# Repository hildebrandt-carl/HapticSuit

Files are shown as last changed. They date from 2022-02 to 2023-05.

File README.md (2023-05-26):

# Mimicking Real Forces on a Drone Through a Haptic Suit to Enable Cost-Effective Validation

Robots operate under certain forces that affect their behavior. For example, a drone meant to deliver packages must hold its pose as long as it operates under its weight and wind limits. Validating that such a drone handles external forces correctly is key to ensuring its safety. Nevertheless, validating the system's behavior under the effect of such forces can be difficult and costly. For example, checking the effects of different wind magnitudes may require waiting for the matching outdoor conditions or building specialized devices like wind tunnels. Checking the effects of different package sizes and shapes may require many slow and laborious iterations, and validating the combinations of wind gusts and package configurations is often hard to replicate. This work introduces a framework to overcome such challenges by mimicking external forces exercised on a drone with limited cost, setup, and space. The framework consists of a haptic suit device consisting of directional propellers that can be mounted onto a drone, a component to transform intended forces into setpoints for the suit's directional propellers, and a controller for the suit to meet those setpoints. We conduct a study to assess the framework's capabilities under multiple scenarios involving various forces. Our findings show that the haptic suit framework can recreate real-world forces on the drone with acceptable precision.

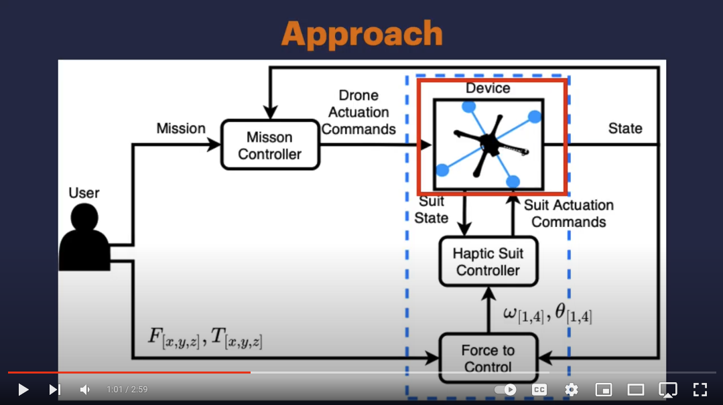
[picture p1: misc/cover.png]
Video (https://youtu.be/5_QmRLWMhes)


## Prerequisites

### Hardware

This software was developed, run and test on the following machines. 

| Computer | CPU | CPU Cores | RAM | Operating System  |
|---|---	|---	|---	|--- |
| Computer 1 | AMD Ryzen Threadripper 3990X | 128 | 128 GB | Ubuntu 20.04 |
| Computer 2 | Intel Core i7-10750H | 12 | 16 GB | Ubuntu 20.04 |

### Software

We require that you have [ROS Noetic](http://wiki.ros.org/noetic/Installation) to operate the drone. We require that you use the [Arduino IDE](https://www.arduino.cc/en/software) for flashing the haptic suit controllers. Finally we require that you have [SOLIDWORKS](https://www.solidworks.com) and a 3D printer for printing the arms of the haptic suit. Finally we require that you have [Matlab](https://www.mathworks.com/products/matlab.html) for computing the inverse kinematics.

## Getting Started

| Component 	| Description 	| Link 	 |
|---	|---	|--- |
| Kinematics 	 | This will describe how we implemented the kinematics and includes Matlab code used to solve the inverse. 	| [README.MD](./kinematics/README.md) 	|
| Physical Design | This includes the designs for the physical arms, battery holders, and pendulum used in our study. 	| [README.MD](./physical_design/README.md)  |
| Drone Workspace 	| This has the software used to fly the drone in each of the scenarios listed in the paper. 	| [README.MD](./drone_ws/README.md) |
| Firmware 	| This describes how to flash the firmware used by the haptic suit | [README.MD](./firmware/README.md) 	 |
| Paper 	 | Includes the paper published at [ICRA 2023](https://www.icra2023.org) | [Paper.pdf](./paper/HapticSuit.pdf) 	|

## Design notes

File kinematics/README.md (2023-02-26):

# Kinematics

This contains the kinematics used convert a force into 4 motor speeds and directions. 

## Derivation

This contains the workings out for how the equations were derived. We started first using a single motor, then computing how it would change if it were allowed to rotate. Next we looked at how 2 motors would behave, and then finally 4 motors. The final equations are shown below:

4 Motors

## Matlab

Next we include the code used to compute the inverse kinematics. To run this open it in matlab and click the green arrow.

### Plotter

Finally we include the code used to plot the force and motor combinations. To run this use the following:

```bash
python animtated_plot.py
```

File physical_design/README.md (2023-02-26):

# Physical Design

This provides both the SOLIDWORKS and SDL files used to 3D print our haptic suit. Each of these were developed to connect DJI Flame Wheel F450. We provide the following:
* Haptic suit arm
* Battery holder
* Pendulum

## Haptic Suit Arm

The blue dashed lines show two arms. To print each arm you can use the following components:

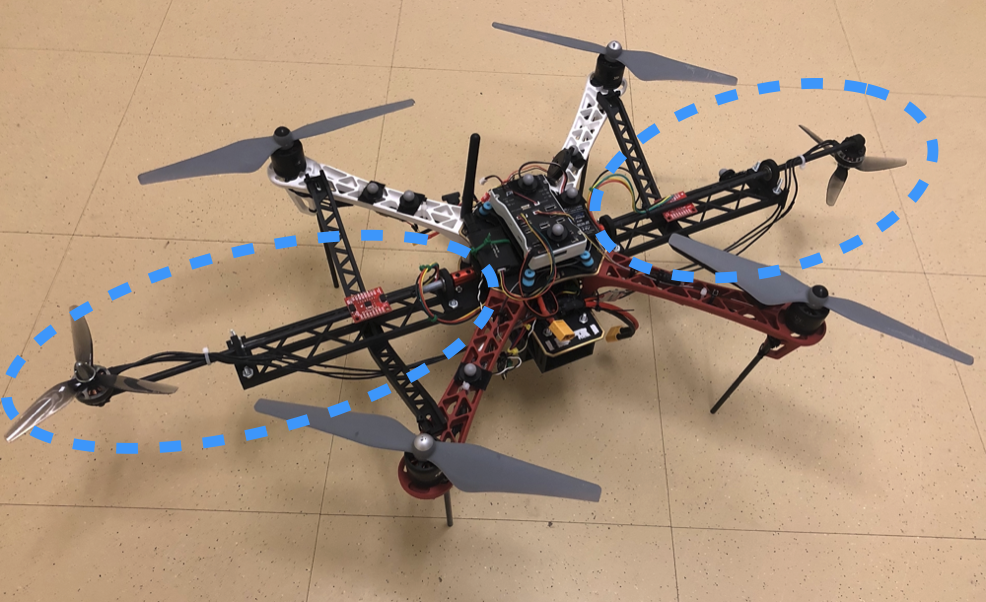
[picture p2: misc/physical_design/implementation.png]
Arms


### Arm

This is the main structure that extends outwards from the body of the drone.

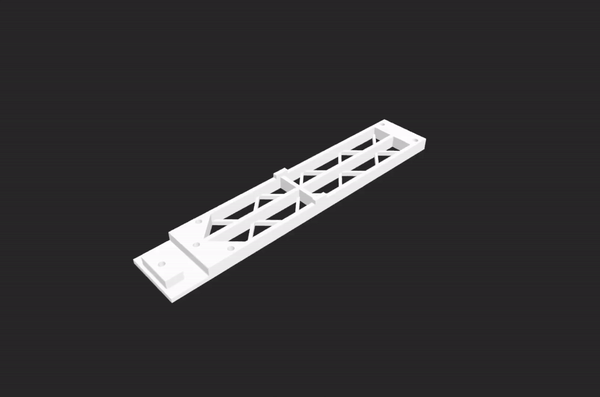
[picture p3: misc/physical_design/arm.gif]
Arm


### Arm Clip

This clips between the arm and the frame, to lock the arm to the frame of the quadrotor.

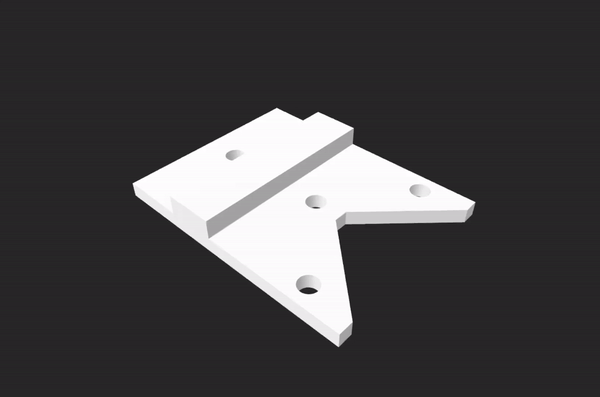
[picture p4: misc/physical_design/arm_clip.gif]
Arm Clip


### Arm Support

This connects to each of the quadrotor arms to add additional support

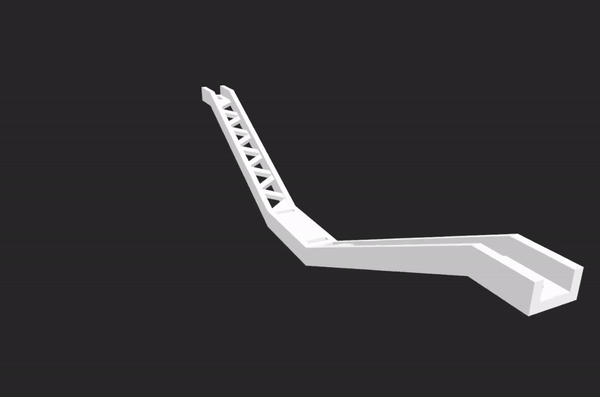
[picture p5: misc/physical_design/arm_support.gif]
Arm Support


### Arm Motor Holder

This sits at the beginning of the arm, and holds the motor used to rotate the direction of the force generated.

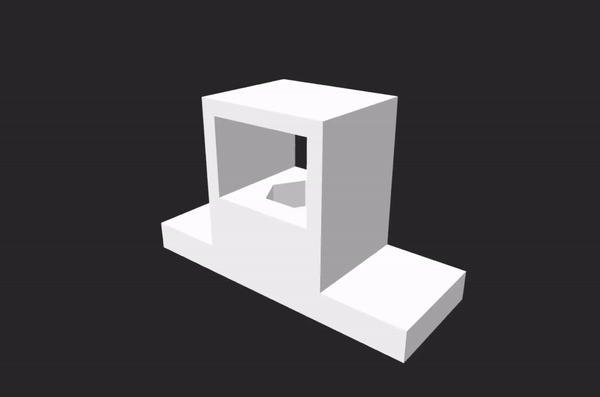
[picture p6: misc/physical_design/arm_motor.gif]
Arm Motor Holder


## Battery Holder

The battery holder sits underneath the drone and holds the battery for both the haptic suit and the quadrotor.

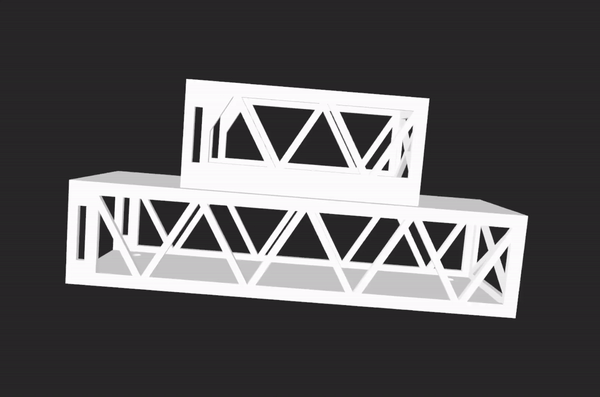
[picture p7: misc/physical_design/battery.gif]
Battery Holder


## Pendulum

The pendulum used in the study was also 3D printed. It consists of two parts. 

### Hinge

First the hinge which is that attached to the drone.

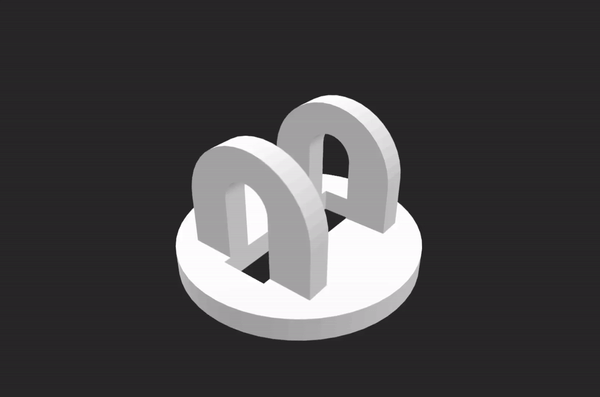
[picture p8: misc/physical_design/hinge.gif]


### Connector

Second the connector which sits inside the hinge.

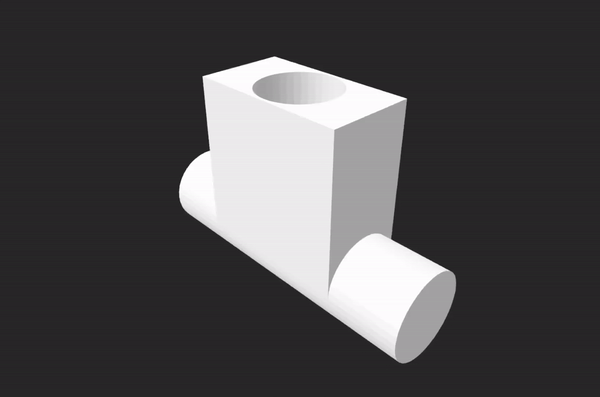
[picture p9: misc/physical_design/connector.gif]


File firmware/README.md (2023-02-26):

# Firmware

To flash the firmware you need to use the [Arduino IDE](https://www.arduino.cc/en/software). This also includes our PID class shown below:

```c
#include <math.h>
#include <Arduino.h>

// A class to compute the control signal
class PID{
  private:
    float Kp ;
    float Ki ;
    float Kd ;
    float dt ;
    float integral;
    float previous_error;

  public:

  // Constructor
  PID()
  {
    Kp = 0;
    Ki = 0;
    Kd = 0;
    dt = 0;

    // Variables used by the controller
    integral = 0;
    previous_error = 0;
  };

  // Constructor
  PID(float Kp_in, float Ki_in, float Kd_in, float rate_in)
  {
    Kp = Kp_in;
    Ki = Ki_in;
    Kd = Kd_in;
    dt = 1.0  / rate_in;

    // Variables used by the controller
    integral = 0;
    previous_error = 0;
  }

  // A function to set the parameters
  void set_parameters(float Kp_in, float Ki_in, float Kd_in, float rate_in)
  {
    Kp = Kp_in;
    Ki = Ki_in;
    Kd = Kd_in;
    dt = 1.0  / rate_in;
  }

  // A function to compute the control signal
  float get_output(float setpoint, float current_output)
  {

    // Create the output
    float output;

    // Run the controller
    float error = setpoint - current_output;
    integral = integral + error * dt;
    float derivative = (error - previous_error)/dt;
    output = Kp*error + Ki*integral + Kd*derivative;
    previous_error = error;

    // Return the output
    return output;
  }
  
};
```

This was used to control both the angle of each of the arms. Please refer to the Arduino documentation for further information on how to flash each of the different boards.

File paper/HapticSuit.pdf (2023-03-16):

## Mimicking Real Forces on a Drone Through a Haptic Suit to Enable Cost-Effective Validation

Carl Hildebrandt¹

, Wen Ying¹

, Seongkook Heo¹

, and Sebastian Elbaum¹

Abstract— Robots operate under certain forces that affect their behavior. Consider, a drone meant to deliver packages must hold its pose as long as it operates under its weight and wind limits. Validating that such a drone handles external forces correctly is key to ensuring its safety. Nevertheless, validating the system’s behavior under the effect of such forces can be difficult and costly. For example, checking the effects of different wind magnitudes may require waiting for the matching outdoor conditions or requiring wind tunnels. Checking the effects of different package sizes and shapes may require many slow and laborious iterations, and validating the combinations of wind gusts and package configurations is often hard to replicate. This work introduces a framework to overcome such challenges by mimicking external forces exercised on a drone with limited cost, setup, and space. The framework consists of a haptic suit device with directional propellers that can be mounted onto a drone, a synthesizer to transform intended forces into setpoints for the suit’s directional propellers, and a controller for the suit to meet those setpoints. We conduct a study to assess the framework’s capabilities under multiple scenarios involving various forces. Our findings show that the haptic suit framework can recreate real-world forces on the drone with acceptable precision.

I. INTRODUCTION
Drones are incredibly versatile, allowing them to complete a multitude of missions in a variety of environments. They can carry sensors and objects [1], [2], balance inverted pendulums [3], [4], juggle balls [5], [6], grasp or push objects [7], [8], or take off from underwater [9]. Throughout all these missions, external forces are exerted on the drone. Carrying weights adds a downwards force, hanging pendulums introduce a swinging force, juggling balls create an intermittent impact force, grasping objects adds a downwards and rotational force, and taking off from underwater adds a resistive force that is removed once in the air.
Validating that drones can adequately behave under those external forces is critical to ensure their correct and safe operation. Such validation takes multiple forms, from model simulation, which offers the opportunity to quickly test many variants of the system and approximations of the forces in the environment, to field tests that exercise the entire system in a limited number of real environments with real physical forces. In this work, we focus on the challenge of conducting full system tests carried out in both a lab and in the field. Validating the effect of external forces on drones brings significant challenges. Consider a drone that must hold its pose while delivering cargo. First, precisely validating the

1University of Virginia, USA {hildebrandt.carl, wy7yv, seongkook, selbaum}@virginia.edu
This work was funded in part through NSF grants #1924777 and AFOSR grant #FA9550-21-1-0164.

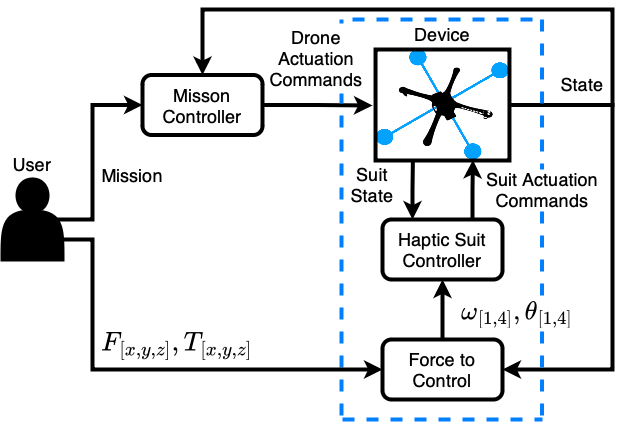
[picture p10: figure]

Fig. 1: Overview of the Haptic Suit Framework

effects of wind would require specialized mechanisms like wind tunnels. Second, validating the space of behaviors would require validating various cargo configurations (e.g., weight, shape). This can be laborious as testers must often set each scenario manually. Third, some forces are extremely difficult to replicate, such as those caused by the subtle combination of gusts of wind and cargo configuration. These challenges make drone behavior validation under external forces costly, difficult, and often infeasible.
In this work, we introduce a framework to address these challenges. Inspired by haptic feedback in interactive systems that simulate forces to provide immersive experiences to users [10], [11], this framework recreates forces on the drone to replicate real-world scenarios. Figure 1 provides an overview of the framework and its three key components:
1) an electro-mechanical device that attaches to the drone under test to provide directional propellers that can generate a rich space of forces and torques; 2) a synthesizer that transforms user-specified force F[x,y,z] and torque T[x,y,z]

functions
into a set of target motor speeds ωi and angles θi for each motor i, using the inverse kinematic equations of the suit; and
3) controllers that read the state of the suit and the drone and use the ωi and θi as setpoints to actuate the suit propellers to match those targets.
The contributions of this work are:
- An innovative concept connecting drone validation and haptic feedback to induce external controlled forces.
- A framework that enables the exertion of a rich set of programmable forces for the validation of drones.
- A study showing that the haptic suit framework can successfully replicate forces from 5 distinct real scenarios.

II. RELATED WORK
Several approaches exist to exercise and manipulate specific external forces on drones. For example, to mimic wind forces, various forms of fans [12], and wind tunnels [13], [14], [15] have been proposed, offering trade-offs between cost, flexibility, and accuracy in the forces being exercised. Similarly, to mimic payloads, it is relatively common to build devices that enable the attachment of different masses with varying volumes [16], [17]. In this case, the level of control can be accurate but often requires a manual setup [18]. Beyond simple forces, we find that general mechanisms for applying forces to a drone are lacking.
In this paper, we aim to accurately mimic more complex external forces without needing expensive setups and laborious procedures. Although not pursuing the same goals, the closest line of work comes from the variety of testbeds meant to support drone development [19], [20], [21], [22], [23]. This work aims to secure the drone such that it can not crash while allowing for some form of movement. For example, Ding et al. proposed using a humanoid arm to hold a drone while it is flying. The goal was to secure the drone while minimizing the effect of this connection [23]. While the purpose of this work was not to exert forces on the drone, one could imagine that with adjustments to the controller function, as well as the development of a new set of kinematics, one could recreate larger forces with precision. Still, these devices are complex and expensive, and for most of the forces we intend to mimic, it would be bounded by the arm’s reach, degrees of freedom, and velocities, while our haptic suit does not have those limitations.
Another related line of work that in part inspired this work is in the area of haptics. Researchers have shown that propeller-based propulsion can be used to produce highfidelity directional force feedback and provide realistic force feedback to its users [10], [11]. However, these methods are designed for handheld use, and their use for robot testing has not been investigated. The closest line of work mimics real sensor values on drones to provide a mix of real world and simulated sensor data [24], [25], [26]. However, this work lacks the ability to exert actual forces onto the drone.

III. FRAMEWORK
The framework aims to mimic the forces a drone may experience during flight, enabling engineers to validate their drones under various scenarios more efficiently, quickly, and easily. We now describe its key components in more detail.
A. Haptic Suit Device
The following requirements guided the haptic suit design. First, the device needed to generate forces with a wide range of magnitudes and directions to support many scenarios (including the ones we later studied). Second, the device needed to mount on the host drone without any point of contact with other external entities in order to reduce flying constraints or interference. Third, the device needed to minimize the disturbance to the drone’s normal behavior to avoid failures that the introduction of the suit may cause.

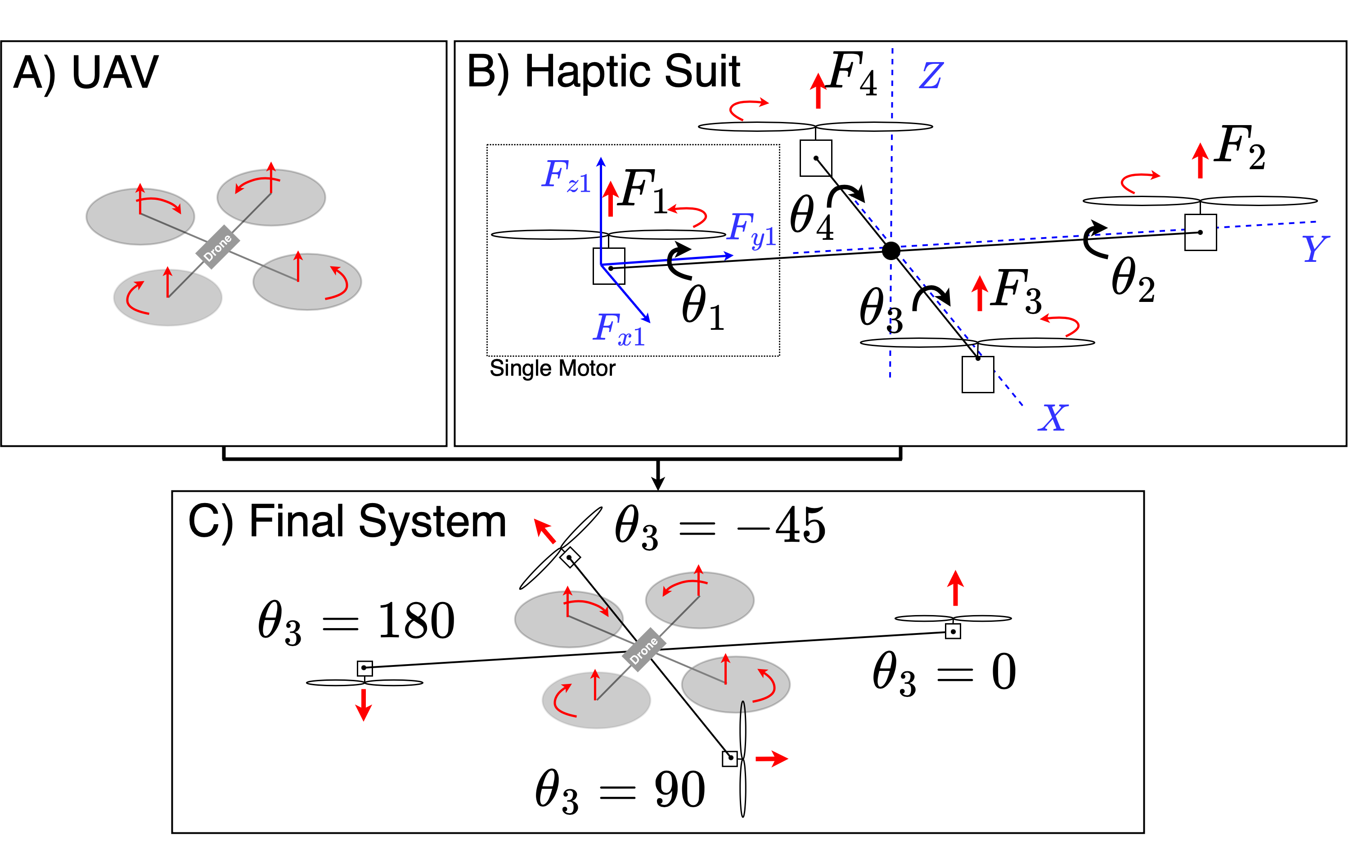
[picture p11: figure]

Fig. 2: Quadrotor, Haptic-Suit, and Haptic-Suit integrated with Quadrotor (grey circles represent quadrotor propellers).

The suit design follows from those requirements. Conceptually, the suit is elegant in its simplicity in that it adopts the host-drone structural design. Without loss of generality and to facilitate the explanation, we exemplify the integration of the haptic suit to a quadrotor as shown in Figure 2. For a quadrotor, shown in Figure 2-A, the suit device consists of four arms, each one with a rotor at its end, as shown in Figure 2-B, reflecting the design of the drone. In the suit, each of the i (i = 4 for quadrotor) rotor’s thrust Fi and torque values Ti can be independently controlled by varying the motor speed ωi

. However, unlike a typical drone where Fi

is
always perpendicular to the drone, the suit can independently rotate each arm by θi
through additional motors at the base of each arm. To allow for precise control, each arm is fitted with an IMU reporting its attitude. This allows us to vary the magnitude of Fi and Ti by varying ωi

, as well as vary
the direction by varying θi
, to create a wide range of forces on the drone regardless of the drone’s current pose.
The integration of the haptic suit and drone is shown in Figure 2-C. The haptic suit is mounted onto the drone with a shift of 45 degrees. This integration meets our requirements in the following ways. First, as each arm has a motor that can independently rotate, it can generate a wide range of forces, allowing for the simulation of a wide range of scenarios. Second, the suit is not attached to anything but the drone, thus not limiting the drone to any specific environment. Third, the suit is symmetrical, lightweight, and has arms that protrude out further than the drone’s arms. This minimizes the changes in both the total and center of mass of the drone while also minimizing interference among airflow through propellers. These design choices reduce the chance that the suit will affect the normal behavior of the drone.
The conceptual design simplicity offers a rich space of trade-offs that will determine the magnitude of the forces that the suit can generate. For example, more powerful motors can generate greater forces. However, their weight, the weight of the arms required to support them, and the battery requirements may undermine some of the forces they can generate and the preciseness of the overall force manipulation. The arms’ length and rotational speed can also affect the type and magnitude of forces that can be applied. This also indirectly affects the airflow of the other drone’s rotors. The profile of all these elements can affect the dynamics of the drone, from adding weight to changing the drag coefficients. We will discuss the particular choices we made for one instantiation of the framework under Section III-F.
B. Force to Control Set Points

Given a haptic suit device, the framework must convert a set of user-defined forces F[x,y,z] and torques T[x,y,z]

into a
set of motor speeds ω[1,4] and rotations θ[1,4]
. For example,
if a user wants to simulate carrying a package, which is equivalent to applying negative force in the Z direction (−Fz), we would need all motors to spin at equal speeds (ω1 = ω2 = ...) such that they generate a force of the correct magnitude (Fz). Furthermore, each of the motors would also need to be pointing directly downwards (θ[1,4] = 180), so that the direction of the force is in the same direction as gravity (−Fz) to exert the same force as a package. Similarly, if a user wants to mimic a horizontal wind with a force Fy, whose magnitude is the same as that of the first example, then motors 2 and 3 would need to create forces in the Fy plane by rotating (θ[3,4] = 90), and each would need to operate at double the speed of the first example to compensate for the lack of motors 1 and 2.
To perform such conversion computations, we define a set of kinematic equations for the haptic suit. Consider motor1 in Figure 2-B, with target speed ω1 and rotation θ1. The force F1 and torque T1 generated by that motor are F1 = kf × ω1 and T1 = km×ω1 where kf and km are the proportionality constants for thrust and moments respectively [27]. Since the capability to rotate the motor affects the forces and torques direction, we must decompose F1 and T1 into (Fx1,Fy1,Fz1) and (Tx1,Ty1,Tz1). Equations 1 showcase the decomposition of F, with similar equations holding for T.

Fx1 = −F1 ×sin(θ1); Fy1 = 0; Fz1 = F1 ×cos(θ1) (1)

We can now generalize these equations to a full suit as per Equations 2.

Fxi = −Fi ×sin(θi);Fyi = 0;Fzi = Fi ×cos(θi) : i ∈ [1,2]

Fxi = 0;Fyi = −Fi ×sin(θi);Fzi = Fi ×cos(θi) : i ∈ [3,4]

(2)

These equations are derived from Equation 1 and thus Fyi = 0 for motors 1 and 2, while Fxi = 0 for motors 3 and 4, as these motors are incapable of rotating in the Y and X planes respectively. To compute torque we use a similar derivation except that since motors on opposite sides of an arm rotate opposite each other, their torque cancels out, so the terms for T2 and T4 are negated.
The final step is to compute the total force Fx,Fy,Fz as per Equation 3. Computing the torques Tx,Ty,Tz must take into consideration the additional torque placed on the system by any unbalanced forces in any given directions. For example, a torque around the X axis can be created by an imbalance of the forces in the Z direction between motors 1 and 2.

F[x,y,z] =

4
∑

i=1

F[x,y,z]i

(3)

To obtain the speed and rotations needed to generate a given force and torque, we compute the inverse kinematics. Given the complexity of the equations and the fact that the number of degrees of freedom is different from the number of variables, we approximate the inverse using numerical methods described in more detail in the implementation.

Tx =

4
∑

i=1

Txi + (Fz1 −Fz2)

Ty =

4
∑

i=1

Tyi + (Fz3 −Fz4)

Tz =

4
∑

i=1

Tzi + ((Fx1 −Fx2) + (Fy3 −Fy4))

(4)

C. Controller
The final step is to actuate each of the suit’s motors and arms into the correct configuration. The framework uses two traditional PID closed-loop controllers per arm. The first controls the motor speed, using the current motor speed as feedback, while the second uses the IMU attitude information as feedback. Note that having an IMU on each arm allows the framework to control the haptic suit independently of the drone’s pose and behavior, which allows users to define forces in the world frame while ignoring the drone’s pose. The set points are given by ω[1,4] and θ[1,4] produced by the previous framework component.
D. Generality
As defined, the framework can be directly instantiated to support multiple drone configurations under two conditions:
1) the device placement can coincide with the drone’s center of mass, and 2) a symmetrical distribution of suit motors is a good fit for the drone structure and the intended forces and torques. As part of the framework presentation we introduced a 4-motor-suit configuration that fits, for example, common quadcopters and octocopters, in the following study we use a 2-motor-suit configuration that suffices to explore the target scenarios on a quadcopter, and extensions to more motors should be trivial to instantiate reusing a similar suit structure (with different motors and arms’ length), body of kinematic equations, and controllers.
E. Limitations and Trade-offs
The haptic framework’s range of forces is constrained by two factors. The first results from the suit design, which mimics a typical drone. Drones control yaw by varying the speeds of motors that spin in opposite directions. A speed imbalance will produce a non-zero overall torque, resulting in a yaw. Three things occur when our suit rotates an arm, as seen in Equation 4. First, as the arm rotates, the force component in the Fz direction will decrease, resulting in a roll or pitch. Second, the arms rotation will induce a Fx, or Fy component, resulting in additional yaw. Third,

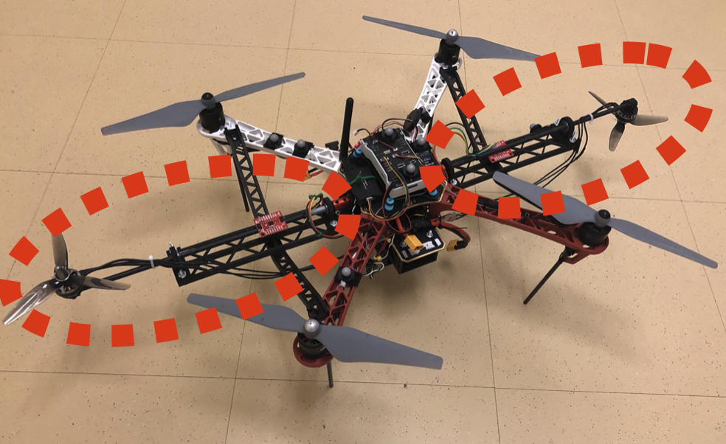
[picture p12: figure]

Fig. 3: Two-arm haptic suit prototype (marked using dashed lines) mounted on a DJI Flamewheel F450 drone [28].

the torque generated by the motor’s spin will also become imbalanced, adding additional roll, pitch, or yaw depending on the rotation. Therefore while we can generate a force in any direction, some forces may result in rolls, pitches, or yaws that can be modeled and should be monitored.
The second results from mounting the suit onto the drone. The drone’s design and capabilities (e.g., weight, footprint, lift, controller) and its tolerance for the unintended perturbations caused by the suit (e.g., interference with airflow, additional weight) directly affect the design of the suit (e.g., the motors it can carry, the propellers dimension, power supply, the arms’ length) and thus the magnitude of the forces our haptic suit can produce.
F. Implementation
Our implementation, which is publicly available¹
, uses
a DJI F450 [28] with a Pixhawk controller [29] governed by the Freyja mission controller [30]. The experiments only required operation in the XY-plane and thus only required a suit with 2 arms. Since the drone’s arms are 25cm, to minimize airflow interaction, we used 5mm-diameter and 29cm length carbon fiber tubes. Each arm connects to a DC motor for rotation driven by a dual-motor driver (Adafruit TB6612). Each arm also has an IMU (SparkFun BNO080) to determine its current rotation angle. 3D-printed components were used to firmly attach the suit to the drone.
The Flamewheel can carry up to 1kg of payload with limited noticeable behavioral changes, which drove the selection of components. We used two tri-blade propellers (length: 5 inch, pitch: 4 inch) and two brushless motors (GARTT ML2204S 2300KV) that are driven by two electronic speed controllers (HGLRC 30A) to generate thrusts. The brushless motors are connected to two UXCELL GA12-N20 DC motors with reduction gears (6V, 70 RPM). Each motor was connected to the end of the carbon fiber tube. The DC and brushless motors were controlled using an Adafruit Feather M0, to which the user could send commands over WiFi. We equipped the suit with its own battery to avoid affecting the drones’ behavior by sharing a power source. The suit, including battery, weighed under 800 grams to minimize the effects on the drone’s behavior.
The remaining components are implemented on top of the Robotic Operating System (ROS) [31] as nodes developed

1https://github.com/hildebrandt-carl/HapticSuit

TABLE I: The force and torques used by each scenario.

Scenario | Force and Torque (Newtons)
Weight (Indoor) | Fz = −3
Steady Wind (Indoor) | Fy = 1
Gusting Wind (Indoor) | Fy = f1([0.5,1]),T[x,y,z] = f2([0.1,0.5])
Pendulum (Indoor) | Fy = f3(ρ),Fz = f4(ρ)
Drop Weight (Outdoor) | Fz = f(t) = ( −5 if 0 < t ≤ 30 0 if t > 30

in Python. The suit PID controllers are implemented on the Adafruit Feather M0. The numerical solver used to compute the inverse kinematics in Matlab [32] was the vpasolver.

IV. STUDY
The study is meant to assess the extent to which the haptic suit framework could mimic real-world forces on a drone.
A. Setup
1) Suit: To assess the haptic suit framework capabilities, we used the prototype described in Section III-F with the suit shown in Figure 3. Through a set of empirical calibrations, we set the k f and km of the kinematic model and the controller coefficients introduced in Section III. The synthesizer that transforms forces and torches to motor velocities and rotation angles was executed offline, while the controller was executed online as the scenarios were running.
2) Scenarios: We flew the drone under a series of scenarios, listed in Table I, designed to expose different types of forces. The weight scenario produces a constant force that points in the Z direction. The wind scenarios produce either a constant force in the Y direction, or in the case of the gusting wind a force in the Y direction and torques in the X,Y, and Z direction sampled from a set interval. The pendulum scenario produces a force in the Z and Y direction that varies based on the position of the drone ρ. The scenarios were performed indoors using a motion capture system, Vicon [33], that is capable of measuring the vehicle’s pose at 200Hz with a 5mm accuracy. The outdoor drop-weight experiment follows a piecewise function based on the time t, and measurements were taken based on the commands generated by Ardupilot [34].
For each scenario, we compare the drone’s behavior under the real external forces versus the forces induced by the haptic suit framework. The scenarios with real forces used physical weights, wind generated by fans, and attached pendulums to create a baseline. For the weight scenario, we selected a 100g, 200g, and 300g cargo. For the wind experiments, we used an industrial fan capable of generating gusts of winds up to 4m/s. To create the pendulum scenario, we attached a hinge allowing a unidirectional motion to a carbon fiber rod that carried weights of 100g, 200g, and 300g. For the outdoor drop-weight scenarios, we used 500g cargo that was dropped after a set time interval using a rope connected to a pin which, when pulled, released the weight.
B. Results for Weight Scenario
In this scenario, the drone was set to hover at 1m while carrying a set weight. Each of the experiments was run 5

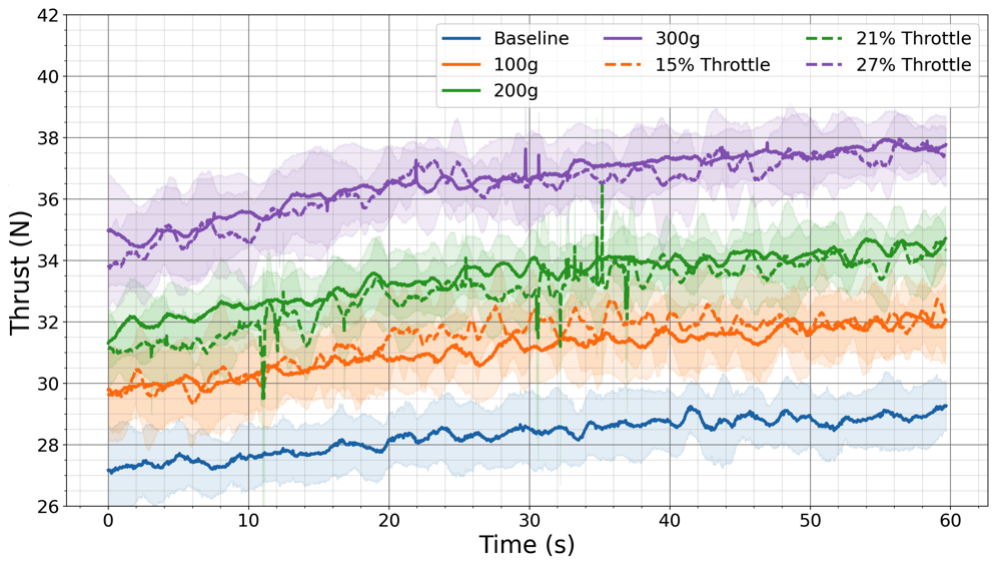
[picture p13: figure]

Fig. 4: Average thrust at different real weights and weights induced by the haptic suit.

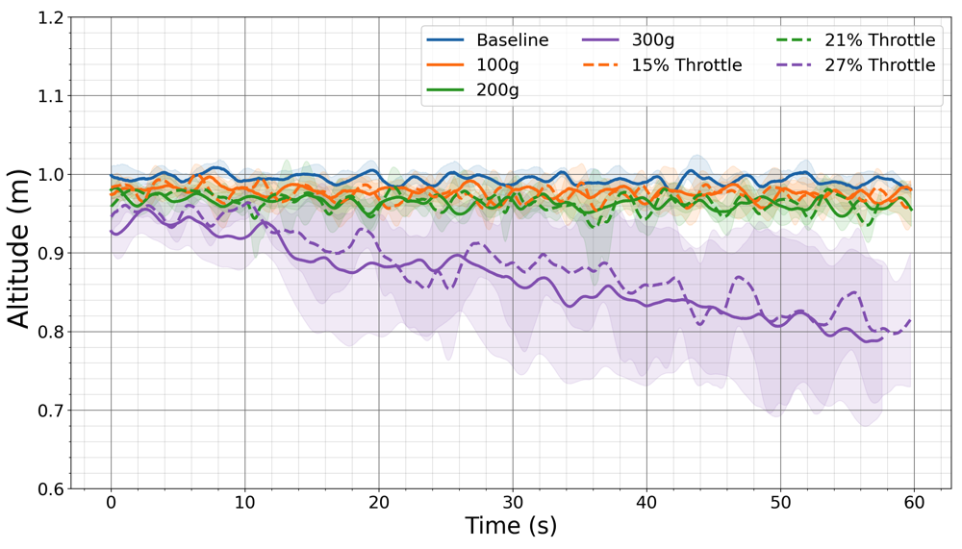
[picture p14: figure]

Fig. 5: Average altitude induced using different real weights and weights induced by the haptic suit.

times for 1 minute. We assess the drone’s behavior in terms of the thrust commands sent by the controller Freyja [30] and the drone’s altitude while carrying different weights. Figure 4 shows the thrust commands sent to the drone by the controller in newtons. Solid lines represent thrust readings using real weights, while dashed lines represent thrust using the haptic suit. As expected, the more weight that is added, the higher the thrust command sent to the drone to maintain altitude. More interestingly, the thrust command’s average and standard deviation are almost identical when using the haptic suit to replicate the real weights. This suggests that, from the drone’s perspective, the suit is exercising almost the same external forces. Figure 5 shows the altitude of the drone as measured by Vicon. The average and standard deviations on altitude are almost identical when comparing the real and the replicated scenarios using the haptic suit. Even the slow decline in altitude at 300g observed in reality, likely caused by an erroneous drone configuration parameter, is replicated when using the haptic suit. Last, the validation with the haptic suit was significantly faster and less errorprone than the real payload, which required frequent stops to remove a weight and secure a new one.

C. Result: Wind Scenarios
We first wanted to explore how the drone would behave under a constant wind force. Testing this often requires an elaborate environment to produce steady wind flows. It is not difficult to conjecture, however, how the drone should behave under a steady wind. We expect that the drone should lean against the wind to maintain its position. Thus, for this

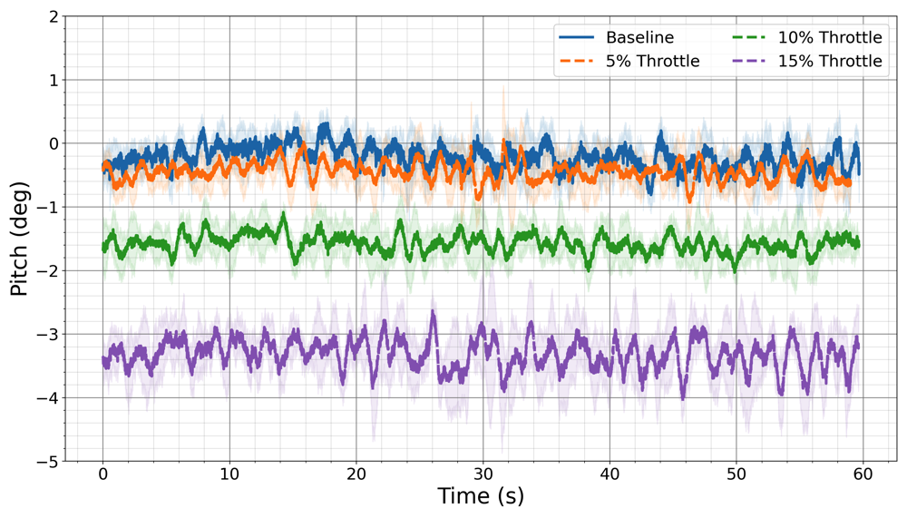
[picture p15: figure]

Fig. 6: Average pitch reported at different constant wind velocities induced by the haptic suit

first wind scenario, rather than testing our drone against a real constant wind, we validated our hypothesis using the haptic suit to replicate the drone operating under steady winds. The test involved increasing the magnitude of the force in the Fy direction using 3 constant values. These correlated with suit throttle values (ω) of 5%, 10%, and 15%. Each of these configurations was run 5 times, and the average and standard deviation of the drone’s pitch is shown in Figure 6. The pitch adjustments of the drone match our conjecture. When the haptic suit’s motors were set to 5%, the pitch was not significantly different from the baseline. However, as the horizontal force placed on the drone grew, the drone made more drastic pitch adjustments to counteract this force. At 15% throttle, which generates a wind equivalent of 1N of force, the drone must almost continuously perform corrections of up to five degrees.
For the varied wind scenario, we rely on industrial fans to mimic wind forces on drones. The airflow in the area where the drone is to hover was recorded between 2.9m/s and 4.1m/s, reflecting the noisy airflow produced. To recreate this scenario using the haptic suit, we randomly varied both

Fy and T[x,y,z]

inside set intervals. Each random sample was selected from a normal distribution to mimic the real wind gusts. The pitch of the drone was then recorded over 5 runs when exposed to the fans and 5 runs when using the haptic suit forces. As shown in Figure 7, the recorded pitch values show a greater amplitude than with the steady wind, as the drone must continuously adjust to different forces to maintain its position. We find that the behaviors are similar when comparing the real wind gusts and the haptic suit-induced ones. However, the haptic suit, on average, produces slightly more pitch than the wind gusts. This is possibly due to slight variations in the drone’s altitude, which would take it in and out of the airflow produced by the fans. This difference points to the limitations of employing such current devices compared with the haptic suit.

D. Results: Oscillating Pendulum Scenario
For this scenario, the drone flies at an altitude of 1m along the x-axis starting at -1m and traversing to 1m before aggressively turning back until it gets to the start point, where it would wait 20 seconds before repeating the process.
To define the forces induced by the pendulum that would

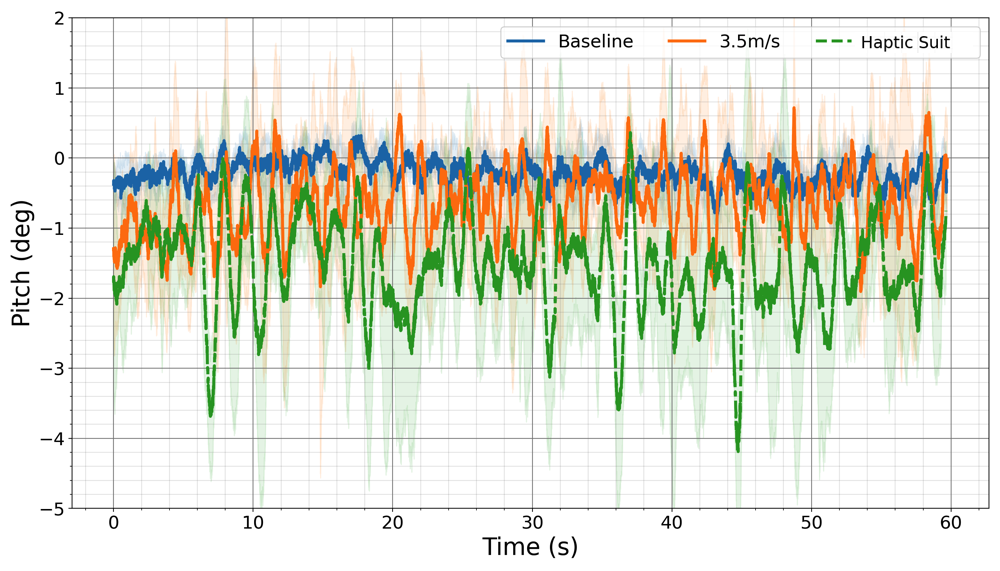
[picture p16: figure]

Fig. 7: Average pitch induced by real fans and haptic suit.

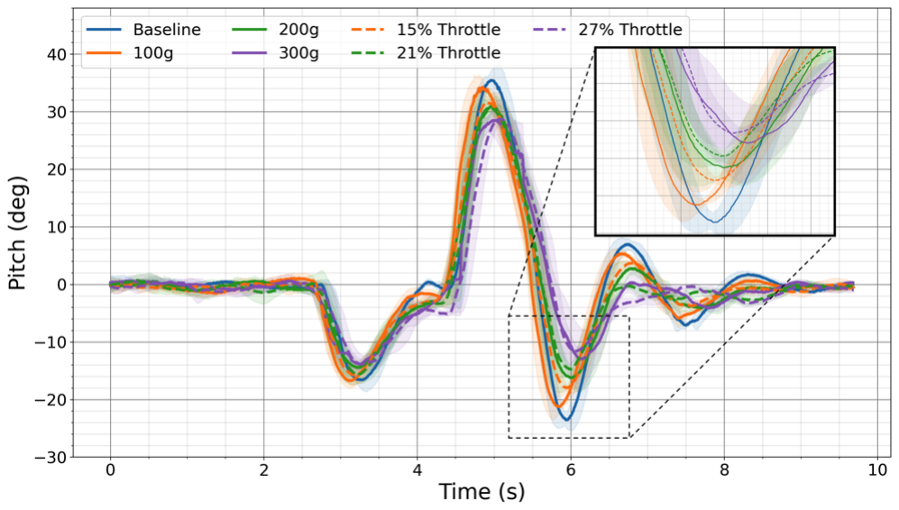
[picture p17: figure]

Fig. 8: Average pitch induced by a pendulum with different weights and haptic suit.

serve as inputs to the haptic suit, we modified OpenAI’s cartpole simulation [35] to match our scenario (our pendulum is facing down, has a range from 0-180 degrees). We modified the simulation to include friction and a PID controller that moved the base of the pendulum to a given setpoint ρ corresponding to the pose of the drone. Thus, the simulation pendulum angle would be updated as the drone moved. The magnitude and direction of the transformed force of the simulator were then sent to the force to control module, which forwarded the correct ω[1,2] and θ[1,2]
to the haptic suit.
Figure 8 shows the drone’s pitch. We were specifically interested in the 6-second mark when the drone tries to become leveled but is affected by the swinging pendulum. We notice how well the haptic suit mimics the real-world forces, with a maximum average difference of 3 degrees at 6s. We conjecture the slight differences observed can be attributed to the simplistic simulation model we used (oversimplified friction approximation) or communication delays (the suit was controlled from a wireless station). Overall, we find it promising that this rather complex scenario can be modeled so accurately using the haptic suit.
E. Results: Drop-Weight
In this outdoor scenario we manually flew the drone to roughly 2m above the ground while using Ardupilot’s altitude hold mode to maintain the drone’s current altitude without any pilot feedback. For the scenario we took off with a payload of 500g attached. After roughly 30 seconds, the payload is released. We expect that as the weight is released there is a sudden change in altitude accompanied by a change in thrust to recover the altitude.

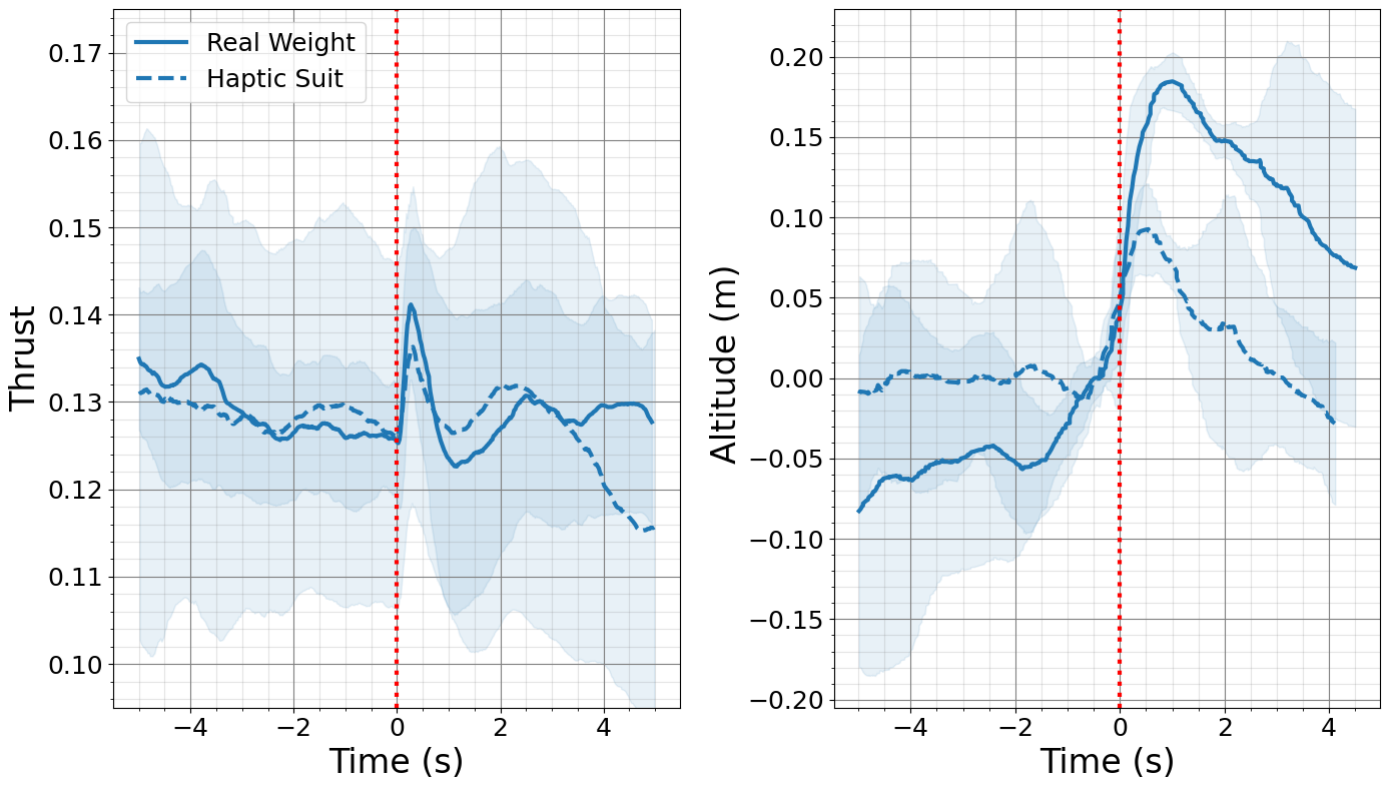
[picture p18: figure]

(a) Average thrust | (b) Average altitude

Fig. 9: Thrust and altitude when dropping real weights and using the haptic suit. Time 0s corresponds to time of weight being dropped.

Figure 9a showcases the average thrust (a unitless value reported by Ardupilot) when using the real weight and the haptic suit approximation, with time 0 corresponding to the weight being dropped. In both cases, when the weight is dropped, there is a spike in thrust. Figure 9b showcases the average altitude changes from the original altitude at the time of dropping weight. As before, when the weight is dropped, there is a sudden increase in altitude when using both the real weight and haptic suit. We notice that when using the real weight, there is a larger increase in altitude likely caused by the friction in the weight release mechanism that was not accounted for in the force functions. This point again highlights one of the advantages of the haptic suit to overcome the limitations of existing practices that would have required a setup that includes a more sophisticated release mechanism to validate the drone’s stability to changes in weights while flying.

V. CONCLUSIONS

We have introduced a haptic suit framework able to exert various forces on a drone as part of its validation. We found that the drone’s thrust, attitude, pose, and behavior under real and haptic suit induced forces appear to be very similar. This provides evidence that the haptic suit can recreate real-world forces on the drone. We also found that surprising behaviors identified under real forces, such as losing altitude in the heavy-weight scenario, are also identified by the haptic suit, providing support for the haptic suit as an effective tool in complementing real-world testing. Last, we found that specific real forces, as simple as a constant wind or as complex as a nonlinear function that changes with the drone state, can be extremely difficult and costly to create in the lab but may be approximated through the suit with limited effort. In future work, we will explore scenarios that require richer functions, such as capturing a moving object in flight, we will create additional suits to fit other drone configurations, and we will extend the application of the suit to validate behaviors involving drone translation so that experiments that currently require large outdoor spaces can be done in the confines of the lab.

REFERENCES

[1] J.-P. Ore, S. Elbaum, A. Burgin, and C. Detweiler, “Autonomous aerial water sampling,” Journal of Field Robotics, vol. 32, no. 8, pp. 1095– 1113, 2015.
[2] E. Beachly, C. Detweiler, S. Elbaum, B. Duncan, C. Hildebrandt,
D. Twidwell, and C. Allen, “Fire-aware planning of aerial trajectories and ignitions,” in 2018 IEEE/RSJ International Conference on Intelligent Robots and Systems (IROS), pp. 685–692, IEEE, 2018.
[3] D. Brescianini, M. Hehn, and R. D’Andrea, “Quadrocopter pole acrobatics,” in 2013 IEEE/RSJ International Conference on Intelligent Robots and Systems, pp. 3472–3479, IEEE, 2013.
[4] M. Hehn and R. D’Andrea, “A flying inverted pendulum,” in 2011 IEEE International Conference on Robotics and Automation, pp. 763– 770, IEEE, 2011.
[5] W. Dong, G.-Y. Gu, Y. Ding, X. Zhu, and H. Ding, “Ball juggling with an under-actuated flying robot,” in 2015 IEEE/RSJ International Conference on Intelligent Robots and Systems (IROS), pp. 68–73, IEEE, 2015.
[6] M. Muller, S. Lupashin, and R. D’Andrea, “Quadrocopter ball jug- ¨ gling,” in 2011 IEEE/RSJ international conference on Intelligent Robots and Systems, pp. 5113–5120, IEEE, 2011.
[7] M. Srikanth, A. Soto, A. Annaswamy, E. Lavretsky, and J.-J. Slotine, “Controlled manipulation with multiple quadrotors,” in AIAA Guidance, Navigation, and Control Conference, p. 6547, 2011.
[8] A. Shankar, S. Elbaum, and C. Detweiler, “In-air exchange of small payloads between multirotor aerial systems,” in International Symposium on Experimental Robotics, pp. 511–523, Springer, 2018.
[9] H. Alzu’bi, I. Mansour, and O. Rawashdeh, “Loon copter: Implementation of a hybrid unmanned aquatic–aerial quadcopter with active buoyancy control,” Journal of field Robotics, vol. 35, no. 5, pp. 764– 778, 2018.
[10] S. Heo, C. Chung, G. Lee, and D. Wigdor, “Thor’s hammer: An ungrounded force feedback device utilizing propeller-induced propulsive force,” in Proceedings of the 2018 CHI Conference on Human Factors in Computing Systems, pp. 1–11, 2018.
[11] S. Je, M. J. Kim, W. Lee, B. Lee, X.-D. Yang, P. Lopes, and A. Bianchi, “Aero-plane: A handheld force-feedback device that renders weight motion illusion on a virtual 2d plane,” in Proceedings of the 32nd Annual ACM Symposium on User Interface Software and Technology, pp. 763–775, 2019.
[12] J. Bannwarth, Z. Chen, K. Stol, and B. MacDonald, “Disturbance accomodation control for wind rejection of a quadcopter,” in 2016 International Conference on Unmanned Aircraft Systems (ICUAS), pp. 695–701, IEEE, 2016.
[13] H. Jeon, J. Song, H. Lee, and Y. Eun, “Modeling quadrotor dynamics in a wind field,” IEEE/ASME Transactions on Mechatronics, vol. 26, no. 3, pp. 1401–1411, 2020.
[14] J. Gonzalez-Rocha, C. A. Woolsey, C. Sultan, and S. F. De Wekker, ´ “Sensing wind from quadrotor motion,” Journal of Guidance, Control, and Dynamics, vol. 42, no. 4, pp. 836–852, 2019.
[15] M. Jurij, E. M. Nor, A. S. M. Rafie, O. F. Marzuki, M. R. Saad, and S. Azrad, “Development and testing of open-jet wind tunnel for quadrotor flight testing,” Journal of Advanced Research in Fluid Mechanics and Thermal Sciences, vol. 64, no. 2, pp. 304–315, 2019.
[16] J. A. Benito, G. Glez-de Rivera, J. Garrido, and R. Ponticelli, “Design considerations of a small uav platform carrying medium payloads,” in Design of Circuits and Integrated Systems, pp. 1–6, IEEE, 2014.
[17] P. E. Pounds, D. R. Bersak, and A. M. Dollar, “Stability of smallscale uav helicopters and quadrotors with added payload mass under pid control,” Autonomous Robots, vol. 33, no. 1, pp. 129–142, 2012.
[18] Windshape, “Services.” http://windshape.com/services/, 2022.
[19] P. Daponte, L. De Vito, F. Lamonaca, F. Picariello, M. Riccio,
S. Rapuano, L. Pompetti, and M. Pompetti, “Dronesbench: An innovative bench to test drones,” IEEE Instrumentation & Measurement Magazine, vol. 20, no. 6, pp. 8–15, 2017.
[20] S. P. Khaligh, A. Mart´ınez, F. Fahimi, and C. R. Koch, “A hil testbed for initial controller gain tuning of a small unmanned helicopter,” Journal of Intelligent & Robotic Systems, vol. 73, no. 1, pp. 289–308, 2014.
[21] N. Xuan-Mung and S.-K. Hong, “A multicopter ground testbed for the evaluation of attitude and position controller,” International Journal of Engineering & Technology, vol. 7, no. 4.39, pp. 65–73, 2018.
[22] Y. Yu and X. Ding, “A quadrotor test bench for six degree of freedom flight,” Journal of Intelligent & Robotic Systems, vol. 68, no. 3, pp. 323–338, 2012.
[23] C. Ding, L. Lu, C. Wang, and J. Li, “6-dof automated flight testing using a humanoid robot arm,” in 2018 IEEE 14th International Conference on Automation Science and Engineering (CASE), pp. 217– 222, IEEE, 2018.
[24] W. Guerra, E. Tal, V. Murali, G. Ryou, and S. Karaman, “Flightgoggles: Photorealistic sensor simulation for perception-driven robotics using photogrammetry and virtual reality,” in 2019 IEEE/RSJ International Conference on Intelligent Robots and Systems (IROS), pp. 6941– 6948, IEEE, 2019.
[25] C. Hildebrandt and S. Elbaum, “World-in-the-loop simulation for autonomous systems validation,” in 2021 IEEE International Conference on Robotics and Automation (ICRA), pp. 10912–10919, IEEE, 2021.
[26] T. Genevois, J.-B. Horel, A. Renzaglia, and C. Laugier, “Augmented reality on lidar data: Going beyond vehicle-in-the-loop for automotive software validation,” in 2022 IEEE Intelligent Vehicles Symposium (IV), pp. 971–976, IEEE, 2022.
[27] K. P. Valavanis and G. J. Vachtsevanos, Handbook of Unmanned Aerial Vehicles-5 Volume Set. New York, NY, USA: Springer, 2014.
[28] DJI, “Flame wheel arf kit.” https://www.dji.com/flame-wh
eel-arf/download, 2022.
[29] Pixhawk, “Pixhawk.” https://pixhawk.org/, 2022.
[30] A. Shankar, S. Elbaum, and C. Detweiler, “Freyja: A full multirotor system for agile & precise outdoor flights,” in 2021 IEEE International Conference on Robotics and Automation (ICRA), pp. 217–223, IEEE, 2021.
[31] M. Quigley, K. Conley, B. Gerkey, J. Faust, T. Foote, J. Leibs,
R. Wheeler, and A. Y. Ng, “Ros: an open-source robot operating system,” in ICRA workshop on open source software, vol. 3, p. 5, Kobe, Japan, 2009.
[32] MATLAB, version 9.12.0 (R2020a). Natick, Massachusetts: The MathWorks Inc., 2020.
[33] V. M. S. Ltd, “Vicon motion capture.” https://www.vicon.com, 2023.
[34] ardupilot, “ardupilot.” https://ardupilot.org, 2022.
[35] G. Brockman, V. Cheung, L. Pettersson, J. Schneider, J. Schulman, J. Tang, and W. Zaremba, “Openai gym,” arXiv preprint arXiv:1606.01540, 2016.

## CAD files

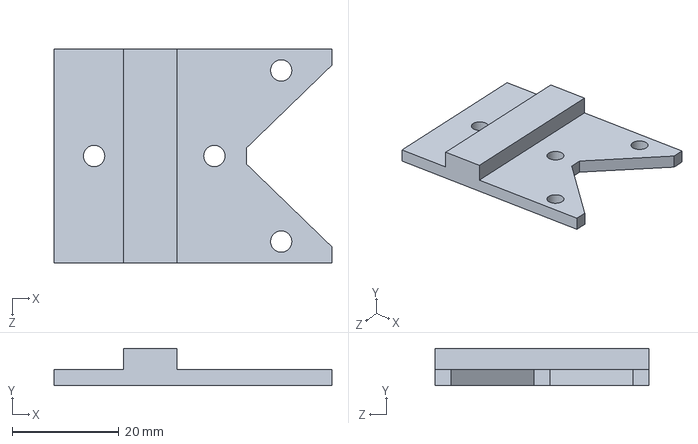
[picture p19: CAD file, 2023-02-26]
physical_design/arm/Lid.SLDPRT
52.0 x 7.00 x 40.0 mm

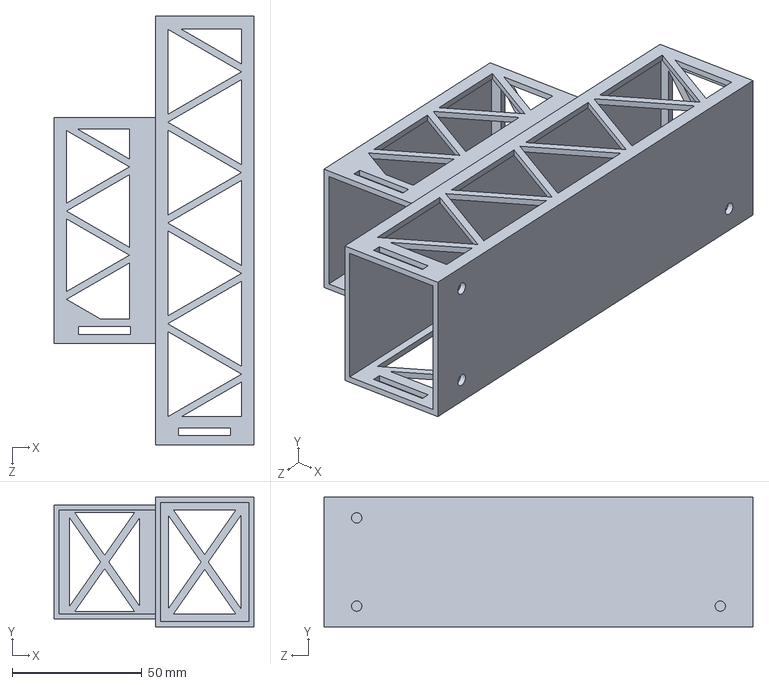
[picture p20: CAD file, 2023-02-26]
physical_design/battery/Battery.SLDPRT
77.0 x 50.0 x 165.0 mm

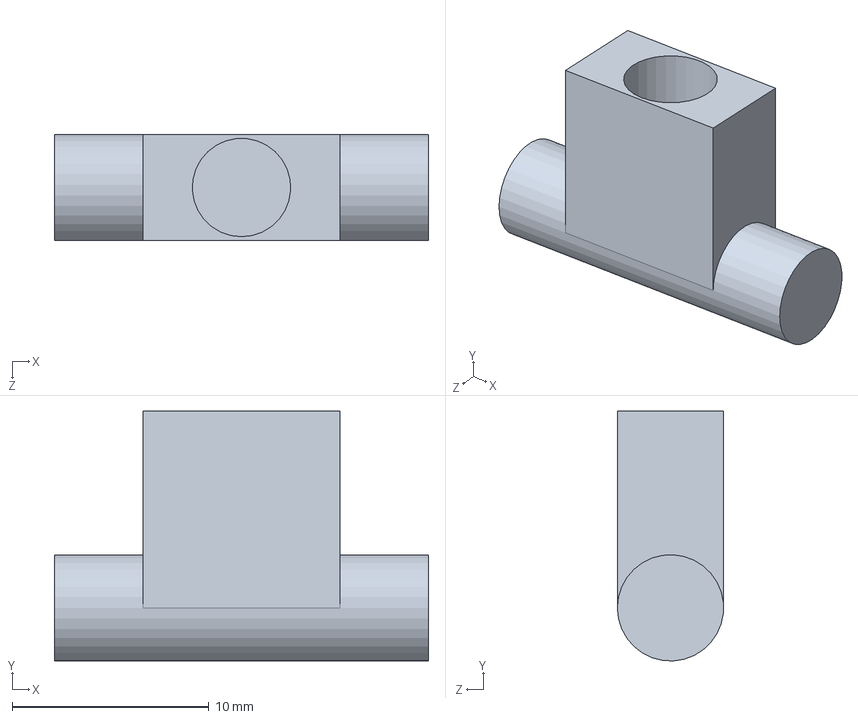
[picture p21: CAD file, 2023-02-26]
physical_design/pendulum/Hinge2.SLDPRT
19.0 x 12.7 x 5.40 mm

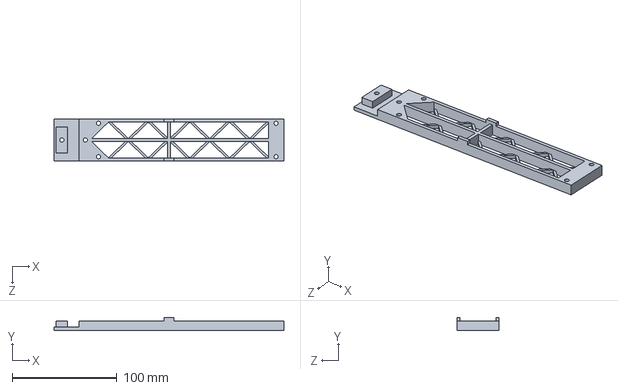
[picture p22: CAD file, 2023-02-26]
physical_design/arm/ExtensionPlate.SLDPRT
220.0 x 12.0 x 40.0 mm

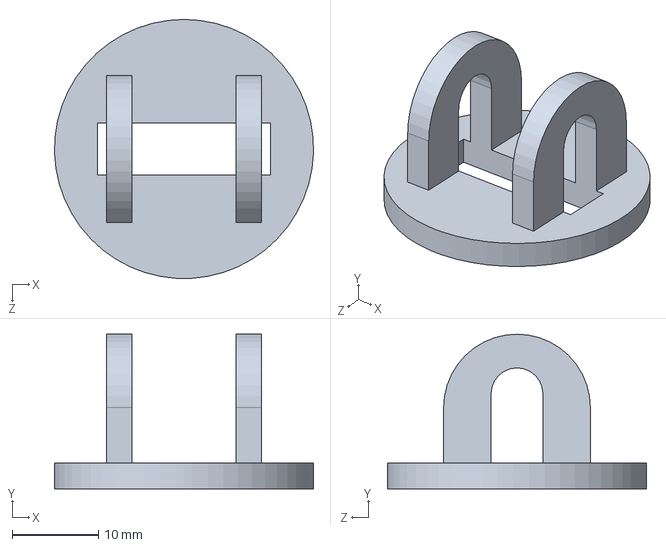
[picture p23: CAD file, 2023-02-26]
physical_design/pendulum/Hinge.SLDPRT
30.0 x 17.9 x 30.0 mm

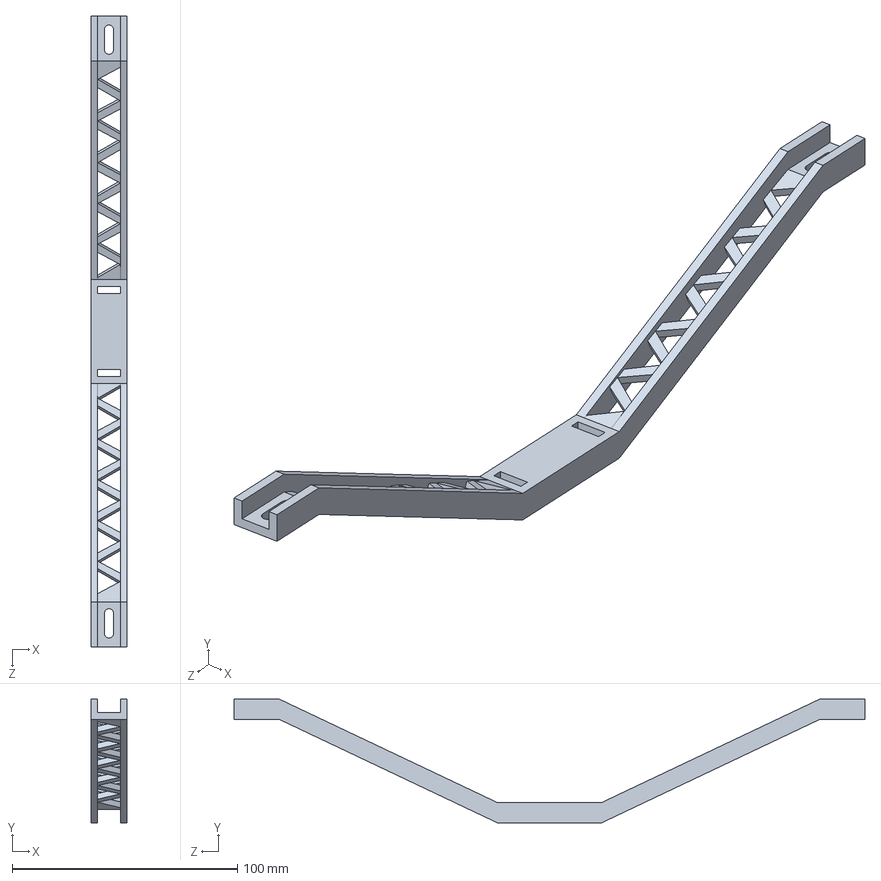
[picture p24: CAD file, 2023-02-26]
physical_design/arm/Support.SLDPRT
16.0 x 55.0 x 280.0 mm

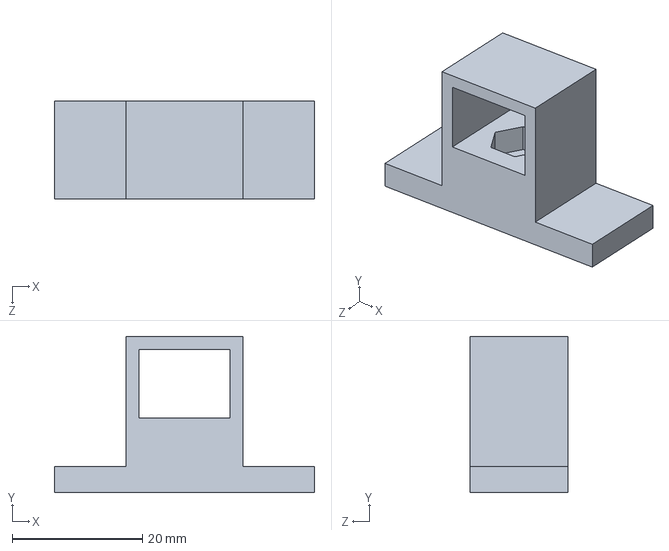
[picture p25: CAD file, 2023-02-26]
physical_design/arm/MotorHolder.SLDPRT
40.0 x 24.0 x 15.0 mm

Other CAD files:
physical_design/arm/ExtensionPlate.STL
physical_design/arm/Lid.STL
physical_design/arm/MotorHolder.STL
physical_design/arm/Support.STL
physical_design/battery/Battery.STL
physical_design/pendulum/Hinge.STL
physical_design/pendulum/Hinge2.STL

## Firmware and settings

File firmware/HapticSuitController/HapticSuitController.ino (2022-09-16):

#include <SPI.h>
#include <Wire.h>
#include <Servo.h>
#include <WiFi101.h>
#include <WiFiUdp.h>
#include "SparkFun_BNO080_Arduino_Library.h" 

// Include the PID class
#include "PID.cpp"

// Define the number of motors
#define NUMBER_ARMS 2
// Define the IMU start address (note they go in decreasing order from this point)
#define IMU_START_ADDRESS 0x4B
// Define the wifi SSID and password (set to "" for no password)
#define WIFI_SSID "ViconNetwork"
#define WIFI_PASSWORD "LessLabUVA1234"
// Define if you want to enable wifi (makes debugging easier)
#define ENABLE_WIFI true
// Define the UDP communication port
#define UDP_PORT 8888
// Define the gear ratio of (1:150) ~70RPM
#define PPR 1050
// Define the looping frequency (HZ)
#define LOOP_RATE 100
// Define the min and max for roll and motor speed
#define ROLL_MAX 270
#define ROLL_MIN -270
#define ROTATION_MAX_SPEED 255
#define ROTATION_MIN_SPEED 20
#define MOTOR_SPEED_MAX 100
#define MOTOR_SPEED_MIN 0

// Define the wifi status
int status = WL_IDLE_STATUS;

// Define variable for communication
unsigned int localPort = UDP_PORT;     
char packetBuffer[SOCKET_BUFFER_UDP_SIZE + 1]; 
char  ReplyBuffer[] = "acknowledged";

// Define the communication protocal
WiFiUDP Udp;

// Define variables for the motors
Servo esc_array[NUMBER_ARMS];
int   roll_setpoint[NUMBER_ARMS]  = {0,0};
int   motor_throttle[NUMBER_ARMS] = {0,0};

// Create the IMU (imu1 goes to 0x4B, imu2 goes to 0x4A)
BNO080 imu_array[NUMBER_ARMS];

// Create variables to hold the IMU data
float current_roll[NUMBER_ARMS];
float previous_roll[NUMBER_ARMS];
float global_roll[NUMBER_ARMS];
int   roll_state[NUMBER_ARMS];

// Declare the pins
const int pwn_pin[] = {5,  11};
const int direction_pin1[] = {12, 14};
const int direction_pin2[] = {6,  13};

// Get the loop rate
const float dt = 1.0 / LOOP_RATE;

// PID class instances
PID pid[NUMBER_ARMS];

// Define setup
void setup()
{
  // Allow time for startup
  delay(1000);

  // Configure communication
  Serial.begin(115200);

  // Start the setup
  delay(5000);
  Serial.println();
  Serial.println("Program Setup Starting");

  // Init variables
  Serial.println("Init variables");
  for(int k = 0; k < NUMBER_ARMS; k++)
  {
    current_roll[k] = 0;
    previous_roll[k] = 0;
    global_roll[k] = 0;
    roll_state[k] = 0;
  }

  // Start wifi
  if (ENABLE_WIFI)
  {
    Serial.println("Setting up WIFI");
    // Configure pins for Adafruit ATWINC1500 Feather
    WiFi.setPins(8, 7, 4, 2);

    // check for the presence of the shield:
    if (WiFi.status() == WL_NO_SHIELD)
    {
      while (1)
      {
        Serial.println("WiFi shield not present");
        delay(10);
      }
    }

    // attempt to connect to WiFi network:
    while ( status != WL_CONNECTED) {
      Serial.println("Attempting to connect to SSID: " + String(WIFI_SSID) + "\n");
      // Connect to the network
      if(strlen(WIFI_PASSWORD) == 0)
      {
        // No password
        status = WiFi.begin(WIFI_SSID);
      } 
      else
      {
        // Password
        status = WiFi.begin(WIFI_SSID, WIFI_PASSWORD);
      }
        
      // wait 10 seconds for connection:
      delay(10000);
    }
    
    // Print you are connected to wifi and print the status (includes the ip address)
    Serial.println("Connected to wifi");
    printWiFiStatus();

    // Start a UDP port to accept commands
    Udp.begin(localPort);
  }

  // Setup the esc motors
  Serial.println("Attaching motors");
  analogWriteResolution(8);
  for(int k = 0; k < NUMBER_ARMS; k++)
  {
    esc_array[k].attach(9+k, 1000, 2000);
    esc_array[k].write(0);

    // Set the different pins
    pinMode(pwn_pin[k],OUTPUT);
    pinMode(direction_pin1[k],OUTPUT);
    pinMode(direction_pin2[k],OUTPUT);
  }
  delay(10);


  // Set the different pins to control the motors
  Serial.println("Creating controllers");
  for(int k = 0; k < NUMBER_ARMS; k++)
  {
    // Set the different PID paramters
    pid[0].set_parameters(10, 0, 0, dt);
    pid[1].set_parameters(10, 0, 0, dt);
  }
  delay(10);

  //Increase I2C data rate to 400kHz
  Serial.println("Increasing I2C rate");
  Wire.begin();
  Wire.setClock(400000);
  delay(10);

  // Start the IMU sensors
  Serial.println("Connecting to IMUs");
  bool imu_success[NUMBER_ARMS] = {false, false};

  // Do this until connection is successful
  while ((imu_success[0] == false) or (imu_success[1] == false))
  {
    // Connect to the IMU
    int imu_address = IMU_START_ADDRESS;
    for(int k = 0; k < NUMBER_ARMS; k++)
    {
      delay(100);
      imu_success[k] = imu_array[k].begin(imu_address);
      imu_address = imu_address -1;
      delay(100);
    }

    if (imu_success[0] == false)
    {
      Serial.println("BNO080 not detected at 0x4B I2C address. Check your jumpers and the hookup guide. Freezing...");
    }
    if (imu_success[1] == false)
    {
      Serial.println("BNO080 not detected at 0x4A I2C address. Check your jumpers and the hookup guide. Freezing...");
    }
    delay(1000);
  }
  
  Serial.println("Enabling rotation Vectors on IMUs");
  // Set IMU's update to 5ms
  for(int k = 0; k < NUMBER_ARMS; k++)
  {
    imu_array[k].enableRotationVector(5);
    delay(10); 
  }

  // Print finished
  Serial.println("Setup finished\n----------------------\n");
}

void loop()
{

  // Start the loop timer
  long start_time = micros();

  // If wifi is available - Check if there is a UDP packet
  if (ENABLE_WIFI)
  {
    int packetSize = Udp.parsePacket();
    if (packetSize)
    {

      // Print the package size and ip address and port
      Serial.println("Received packet of size (" +  String(Udp.remoteIP()) + ") from " +  String(Udp.remotePort()) + ":");

      // Read the packet into packetBufffer
      int len = Udp.read(packetBuffer, SOCKET_BUFFER_UDP_SIZE);
      if (len > 0) packetBuffer[len] = 0;
      Serial.println("Contents:");
      Serial.println(packetBuffer);

      // Get the messages
      char *m1 = sub_str(packetBuffer, 1);
      char *m2 = sub_str(packetBuffer, 2);
      char *m3 = sub_str(packetBuffer, 3);
      char *m4 = sub_str(packetBuffer, 4);
      Serial.println("Received command: " + String(m1) + ", " + String(m2) + ", " + String(m3) + ", " + String(m4));
      
      // Convert to the right value and max sure it stays within the correct bounds
      roll_setpoint[0]  = max(min(atoi(&m1[0]), ROLL_MAX), ROLL_MIN) ;
      roll_setpoint[1]  = max(min(atoi(&m2[0]), ROLL_MAX), ROLL_MIN);
      motor_throttle[0] = max(min(atoi(&m3[0]), MOTOR_SPEED_MAX), MOTOR_SPEED_MIN);
      motor_throttle[1] = max(min(atoi(&m4[0]), MOTOR_SPEED_MAX), MOTOR_SPEED_MIN);
      Serial.println("Accepted command: " + String(roll_setpoint[0]) + ", " + String(roll_setpoint[1]) + ", " + String(motor_throttle[0]) + ", " + String(motor_throttle[1]));

      // Send a reply
      Udp.beginPacket(Udp.remoteIP(), Udp.remotePort());
      Udp.write("Command Accepted\n");
      // Udp.write("Roll Setpoint (" + String(roll_setpoint[0]) + ", " + String(roll_setpoint[1]) + ")");
      // Udp.write("Motor Speed (" + String(motor_throttle[0]) + ", " + String(motor_throttle[1]) + ")");
      Udp.endPacket();
    }
  }

  // Get the latest IMU data
  for(int k = 0; k < NUMBER_ARMS; k++)
  {
    if (imu_array[k].dataAvailable() == true)
    {
      // Get the current roll
      current_roll[k] = (imu_array[k].getRoll()) * 180.0 / PI; 
      // Keep track of the global roll value
      global_roll[k] = update_global_roll(current_roll[k], previous_roll[k], &roll_state[k]);
      // Update the previous roll
      previous_roll[k] = current_roll[k];
    }
  }

  // Loop through the motors
  for(int k = 0; k < NUMBER_ARMS; k++)
  {
    // Compute the roll output
    float motor_power = pid[k].get_output(roll_setpoint[k], global_roll[k]);
    // Serial.println("Motor " + String(k) + " power: " + String(motor_power));

    // Get the sign of the motor_power
    int motor_direction = (motor_power > 0) - (motor_power < 0);
    motor_power = min(abs(motor_power), ROTATION_MAX_SPEED);

    // Check if the motor power is less than a threshold
    if (motor_power < ROTATION_MIN_SPEED)
    {
      motor_power = 0;
      motor_direction = 0;
    }

    // Validate the safe rotation
    if (!rotation_within_bounds(global_roll[k], motor_direction))
    {
      motor_power = 0;
    }

    // Set the motor to rotate
    set_motor(motor_direction, motor_power, pwn_pin[k], direction_pin1[k], direction_pin2[k]);

  }

  // Sets the motor throttle
  for(int k = 0; k < NUMBER_ARMS; k++)
  {
    esc_array[k].write(motor_throttle[k]);
  }
  
  // Maintain the loop rate
  while ((micros() - start_time) <= (dt * 1.0e6))
  {
    ;
  }

  // Serial.println("Motor0: " + String(roll_setpoint[0]) + "/" + String(global_roll[0]) +
  //                "\nMotor1: " + String(roll_setpoint[1]) + "/" + String(global_roll[1]));
  // Serial.println("---------------------");
}

void printWiFiStatus() 
{
  // print the SSID of the network you're attached to:
  Serial.print("SSID: ");
  Serial.println(WiFi.SSID());

  // Print your WiFi shield's IP address:
  IPAddress ip = WiFi.localIP();
  Serial.print("IP Address: ");
  Serial.println(ip);

  // Print the received signal strength:
  long rssi = WiFi.RSSI();
  Serial.print("Signal strength (RSSI):");
  Serial.print(rssi);
  Serial.println(" dBm");
}

// Control the spinning motors
// rotation_direction --> Direction motors spin in, either 1 or -1
//pwm                 --> The pwm value sent to the motor (higher == rotate faster)
void set_motor(int rotation_direction, int pwm, int pwn_pin, int dir_pin1, int dir_pin2)
{
  analogWrite(pwn_pin, pwm);
  if(rotation_direction == 1){
    digitalWrite(dir_pin1, HIGH);
    digitalWrite(dir_pin2, LOW);
  }
  else if(rotation_direction == -1){
    digitalWrite(dir_pin1, LOW);
    digitalWrite(dir_pin2, HIGH);
  }
  else{
    digitalWrite(dir_pin1, LOW);
    digitalWrite(dir_pin2, LOW); 
  }  
}

// Segment the strings
char* sub_str (char* input_string, int segment_number) 
{
  char *act, *sub, *ptr;
  static char copy[100];
  int i;
 
  strcpy(copy, input_string);
  for (i = 1, act = copy; i <= segment_number; i++, act = NULL) 
  {
    sub = strtok_r(act, ",", &ptr);
    if (sub == NULL) break;
  }
  return sub;
}

// Computes the global roll value (i.e removes the 180 discontinuty)
double update_global_roll(double cur_reading, double prev_reading, int* state)
{
  int current_state = *state;
  double diff = cur_reading - prev_reading;
  // If the sign has changed
  if (abs(diff) > 180)
  {
    if (diff > 0)
    {
      // Update the state
      current_state = current_state - 1;
    }
    else
    {
      // Update the state
      current_state = current_state + 1;
    }
  }
  // Save the state
  *state = current_state;

  float global_roll = (current_state * 360) + cur_reading;

  return global_roll;
}

// Need to write a verify safety function here
bool rotation_within_bounds(double current_roll, double current_direction)
{
  bool safe = true;
  if ((current_roll < ROLL_MIN) and (current_direction <= -1))
  {
    safe = false;
  }
  if ((current_roll > ROLL_MAX) and (current_direction >= 1))
  {
    safe = false;
  }
  return safe;
}

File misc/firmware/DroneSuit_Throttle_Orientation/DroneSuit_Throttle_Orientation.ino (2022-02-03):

#include <SPI.h>
#include <WiFi101.h>
#include <WiFiUdp.h>
#include <Servo.h>
#include <Wire.h>

// How many motors
#define NMOTORS 2

int status = WL_IDLE_STATUS;
//#include "arduino_secrets.h"
///////please enter your sensitive data in the Secret tab/arduino_secrets.h
char ssid[]     = "ViconNetwork";   
char pass[]     = "LessLabUVA1234";  
int keyIndex = 0;            // your network key Index number (needed only for WEP)

unsigned int localPort = 8888;      // local port to listen on

char packetBuffer[SOCKET_BUFFER_UDP_SIZE + 1]; //buffer to hold incoming packet
char  ReplyBuffer[] = "acknowledged";       // a string to send back

WiFiUDP Udp;

Servo esc_1;
Servo esc_2;
int throttle1 = 0;
int throttle2 = 0;
int timer = 0;

//70 rpm, around 1:150 gear ratio
const int PPR = 1050;

int angle[NMOTORS] = {0,0};

#include "SparkFun_BNO080_Arduino_Library.h" // Click here to get the library: http://librarymanager/All#SparkFun_BNO080
BNO080 myIMU1; //Open I2C ADR jumper - goes to address 0x4B
BNO080 myIMU2; //Closed I2C ADR jumper - goes to address 0x4A

// A class to compute the control signal
class SimplePID{
  private:
    float kp, kd, ki, umin, umax; // Parameters
    float eprev, eintegral; // Storage

  public:
  // Constructor
  SimplePID() : kp(1), kd(0), ki(0), umin(0), umax(255), eprev(0.0), eintegral(0.0){}

  // A function to set the parameters
  void setParams(float kpIn, float kdIn, float kiIn, float uminIn, float umaxIn){
    kp = kpIn; kd = kdIn; ki = kiIn; umin = uminIn, umax = umaxIn;
  }

  // A function to compute the control signal
  void evalu(float target, float deltaT, int &pwr, int &dir){
    // error
    int e = target;
    
//    Serial.print("target ");
//    Serial.print(target);
//    Serial.print(",");
//    
//    Serial.print("e ");
//    Serial.print(e);
//    Serial.print(",");
  
    // derivative
    float dedt = (e-eprev)/(deltaT);
  
    // integral
    eintegral = eintegral + e*deltaT;
  
    // control signal
    float u = kp*e + kd*dedt + ki*eintegral;
  
    // motor power
    pwr = (int) fabs(u);
    if( pwr > umax ){
      pwr = umax;
    }

    pwr = map(pwr, 0, umax, 0, umax-umin) + umin;
  
    // motor direction
    dir = 1;
    if(u<0){
      dir = -1;
    }
  
    // store previous error
    eprev = e;

//    Serial.print("pwr ");
//    Serial.print(pwr);
//    Serial.print(",");
  }
  
};


//pins
const int pwm[] = {5,11};
const int in1[] = {12,14};
const int in2[] = {6,13};

// Globals
long prevT = 0;

float roll[] = {0.0, 0.0};


// PID class instances
SimplePID pid[NMOTORS];

void setup() {
  //Configure pins for Adafruit ATWINC1500 Feather
  WiFi.setPins(8,7,4,2);

  analogWriteResolution(8);

  esc_1.attach(9, 1000, 2000);
  esc_2.attach(10, 1000, 2000);

  esc_1.write(0);
  esc_2.write(0);
  
  //Initialize serial and wait for port to open:
  Serial.begin(115200);
//  while (!Serial) {
//    ; // wait for serial port to connect. Needed for native USB port only
//  }

  // check for the presence of the shield:
  if (WiFi.status() == WL_NO_SHIELD) {
    Serial.println("WiFi shield not present");
    // don't continue:
    while (true);
  }

  // attempt to connect to WiFi network:
  while ( status != WL_CONNECTED) {
    Serial.print("Attempting to connect to SSID: ");
    Serial.println(ssid);
    // Connect to WPA/WPA2 network. Change this line if using open or WEP network:
//    status = WiFi.begin(ssid);
    status = WiFi.begin(ssid, pass);

    // wait 10 seconds for connection:
    delay(10000);
  }
  Serial.println("Connected to wifi");
  printWiFiStatus();

  Serial.println("\nStarting connection to server...");
  // if you get a connection, report back via serial:
  Udp.begin(localPort);

  Wire.begin();
  Wire.setClock(400000); //Increase I2C data rate to 400kHz

  for(int k = 0; k < NMOTORS; k++){
    pinMode(pwm[k],OUTPUT);
    pinMode(in1[k],OUTPUT);
    pinMode(in2[k],OUTPUT);

//    pid[0].setParams(4,0.2,0,50,255);
//    pid[1].setParams(2,0.1,0,20,255);
    
//    pid[0].setParams(6,0.108,0,0,255);
//    pid[1].setParams(4,0.072,0,0,255);

    pid[0].setParams(4,0.072,0,0,255);
    pid[1].setParams(2,0.036,0,0,255);
  }
  Serial.println("here0\n");

  //Start 2 sensors
  myIMU1.begin(0x4B);
  myIMU2.begin(0x4A);

  Serial.println("here1\n");
  myIMU1.enableRotationVector(5); //Send data update every 5ms
  myIMU2.enableRotationVector(5); //Send data update every 5ms
  Serial.println("here2\n");
}

void loop() {

  Serial.println("loop\n");

  // if there's data available, read a packet
  int packetSize = Udp.parsePacket();
  if (packetSize)
  {
    Serial.print("Received packet of size ");
    Serial.println(packetSize);
    Serial.print("From ");
    IPAddress remoteIp = Udp.remoteIP();
    Serial.print(remoteIp);
    Serial.print(", port ");
    Serial.println(Udp.remotePort());

    // read the packet into packetBufffer
    int len = Udp.read(packetBuffer, SOCKET_BUFFER_UDP_SIZE);
    if (len > 0) packetBuffer[len] = 0;
    Serial.println("Contents:");
    Serial.println(packetBuffer);

    char *m1 = subStr(packetBuffer, 1);
    char *m2 = subStr(packetBuffer, 2);
    char *m3 = subStr(packetBuffer, 3);
    char *m4 = subStr(packetBuffer, 4);

    Serial.println("Values:");
    Serial.println(m1);
    Serial.println(m2);
    Serial.println(m3);
    Serial.println(m4);
    
    throttle1 = atoi(&m1[0]);
    throttle2 = atoi(&m2[0]);
    angle[0] = atoi(&m3[0]);
    angle[1] = atoi(&m4[0]);

    // send a reply, to the IP address and port that sent us the packet we received
    Udp.beginPacket(Udp.remoteIP(), Udp.remotePort());
    //Udp.write(ReplyBuffer);
    Udp.write("m1: ");
    Udp.print(throttle1);
    Udp.write("\t m2: ");
    Udp.print(throttle2);
    Udp.write("\t m3: ");
    Udp.print(angle[0]);
    Udp.write("\t m4: ");
    Udp.println(angle[1]);
    Udp.endPacket();
  }

  //Look for reports from the IMU1
  if (myIMU1.dataAvailable() == true)
  {
    roll[0] = (myIMU1.getRoll()) * 180.0 / PI; // Convert roll to degrees
  }

  if (myIMU2.dataAvailable() == true)
  {
    roll[1] = (myIMU2.getRoll()) * 180.0 / PI; // Convert roll to degrees
  }

   Serial.println(String("roll[1]:\t") + String(roll[1], 2) + "\n"); 

  // set target position
  float target[NMOTORS];
  for(int k=0; k<NMOTORS; k++){
    target[k] = map (angle[k], 0, 180, 0, PPR) - map (roll[k], 0, 180, 0, PPR);
  }

  
  // time difference
  long currT = micros();
  float deltaT = ((float) (currT - prevT))/( 1.0e6 );
  prevT = currT;

  // loop through the motors
  for(int k = 0; k < NMOTORS; k++){
    int pwr, dir;
    // evaluate the control signal
    pid[k].evalu(target[k],deltaT,pwr,dir);
    // signal the motor
    setMotor(dir,pwr,pwm[k],in1[k],in2[k]);
  }

//  Serial.println(throttle1);
//  Serial.println(throttle2);
  esc_1.write(throttle1);
  esc_2.write(throttle2);
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

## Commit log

2022-09-02 Added the kinematics
2022-09-08 Updated with kinematic equation solver using matlab
2023-02-26 Added some documentation
    [Battery.SLDPRT, Battery.STL, ExtensionPlate.SLDPRT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]
